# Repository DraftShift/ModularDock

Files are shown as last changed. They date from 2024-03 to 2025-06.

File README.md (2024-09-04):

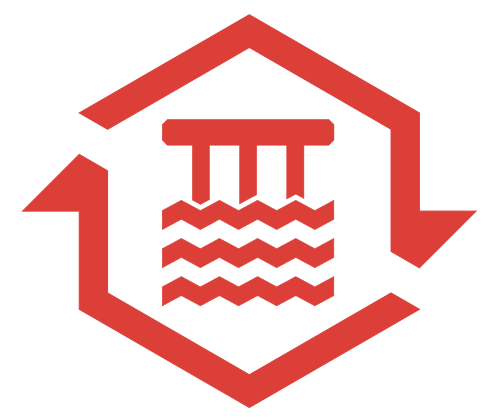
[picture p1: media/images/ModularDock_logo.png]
#  Modular Dock


&nbsp;&nbsp;&nbsp;&nbsp;&nbsp;&nbsp;


**Modular Dock for StealthChanger**

This dock is a drop in type. The back plate will allow for you to adjust the tool to be at perfect 90, I'd recommend 1 degree forward just to keep the dock in place.  Magnets are 5x2s and are optional, but recommened.

See [TODO](TODO.md) before you commit to building these.

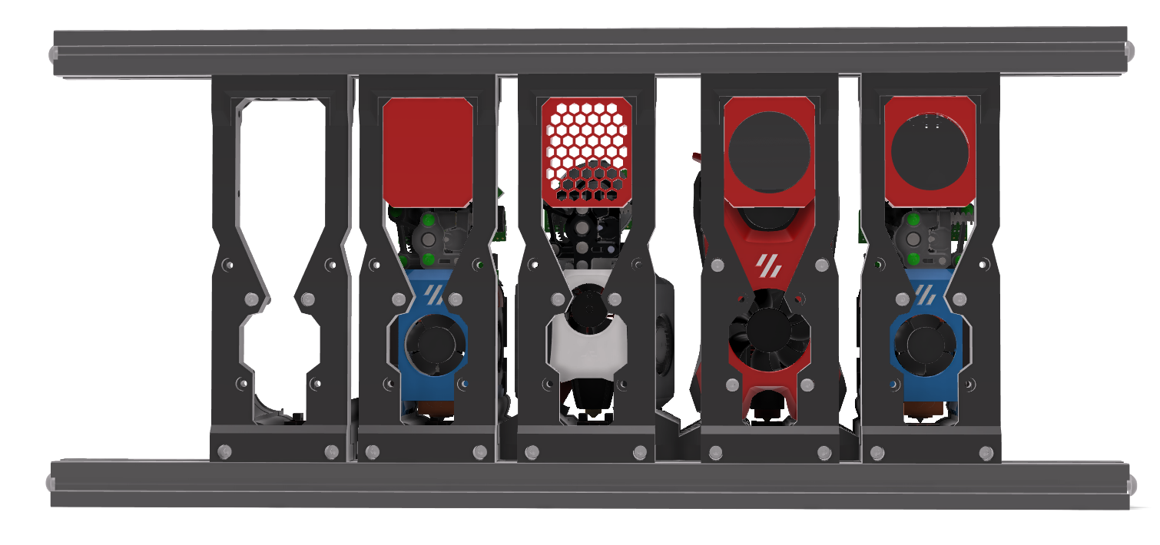
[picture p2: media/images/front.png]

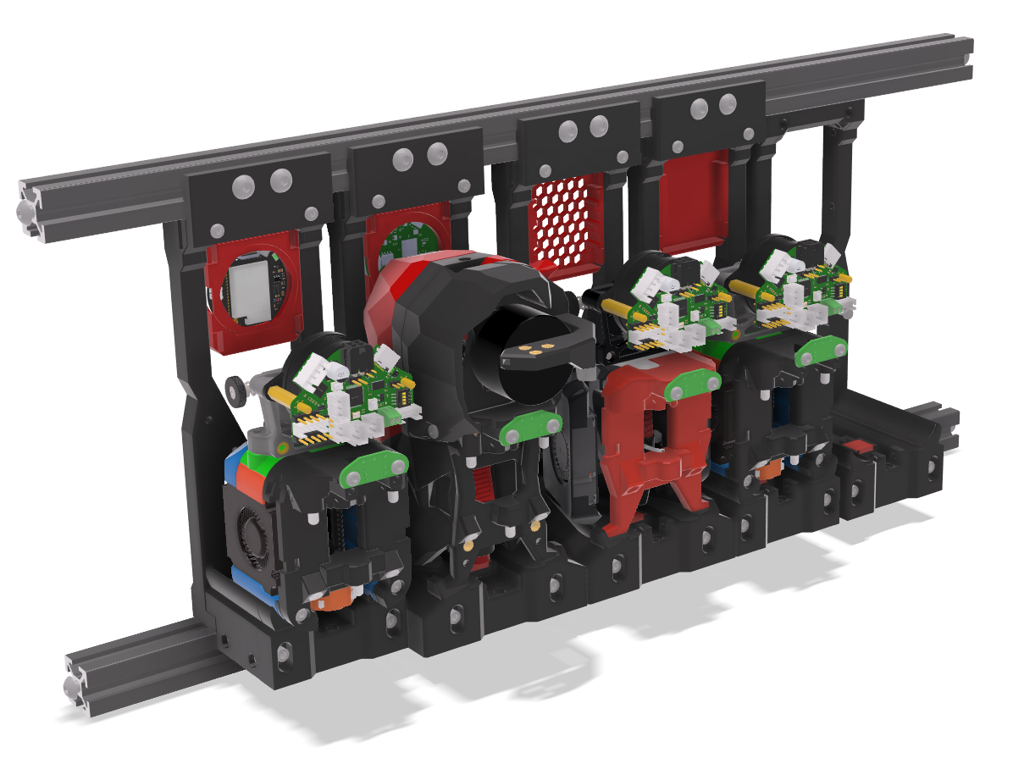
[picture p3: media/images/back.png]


### Orientation

The STLs are not already in the proper orientation

### Print list
- 1 frame (Top, Bottom, Left, Right)
- 1 frame L bracket (optional)
- 1 [tooltype] Base
- 1 [tooltype] Back [type]
- 1 Wiper [type]
- 1 Container [type] (optional)
- Combination of Links (only if not using crossbar for docks)

**NOTE: all docks must end at on the same `Y` length and `Z` height, do not mix dock lengths or heights**

**NOTE: stubby version not compatible with extended frame crossbar versions (2040 front, Door Buffer, etc)**

# BOM

[BOM](BOM.md)

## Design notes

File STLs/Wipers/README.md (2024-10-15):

Bamboo PTFE wiper based on [Bamboo clone wiper](https://www.printables.com/model/359226-bambu-lab-nozzle-wiper)

Leaving the old one here as an alternative but it's much too stiff.

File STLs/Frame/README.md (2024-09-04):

**Short frame should only be used with 1515 printers.  You can use it with 2020 but the Z requirement may pull the MGN block off the rail.  You have been warned, to be safe stick to the normal size frame unless you know what you are doing.**

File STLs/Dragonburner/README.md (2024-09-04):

- Base.stl is for all use cases

- Base_Stubby.stl is **ONLY** to be used with stock frame. ie: Top Mount or MiniBFIs, do not use with Top_Crossbar.stl, Bottom_Crossbar.stl

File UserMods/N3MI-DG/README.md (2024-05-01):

# KNOMI2 Container Mod
Allow the WIFI antenna to be mounted to the back of the container.
Added XH connector.
Added cable tie loop.
Added screws to secure the back plate.
Trimmed sides of frame at extremities of Knomi for cleaner printing.
Added extra clearance around USB port.

#### Extra BOM
2x M2x10mm Self Tapping Screws
1x XH-2A Female Connector
1x Cable Tie

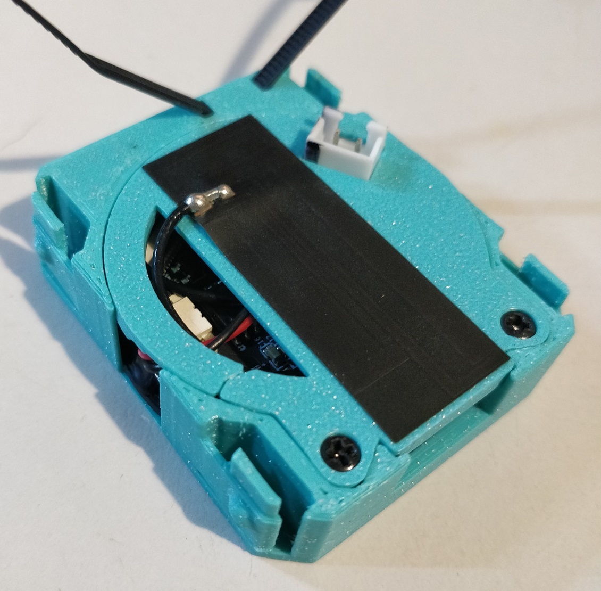
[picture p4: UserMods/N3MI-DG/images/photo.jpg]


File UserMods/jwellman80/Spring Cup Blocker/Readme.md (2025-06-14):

# Spring Cup Blocker

by [jwellman80](https://github.com/jwellman80) aka. averen on most of the Discords. 

This blocker is held up by a short piece of spring steel rather than a spring.  I found that 22mm measured from the center screw was just about right for use with the AntHead docks.  

# BOM

|Part|Amount|Description|
|:---|:----:|:---|
|Spring Steel| 1 | [Amazon](https://www.amazon.com/SunplusTrade-Stainless-Exhaust-Multi-Purpose-Locking/dp/B072WC1MXT) |
|M2x4 Screw| 1 | [Amazon](https://www.amazon.com/dp/B0C5JVC6Z3)|

The Spring Steel and Screws can likely be anything that fits.  Above is just what I used.  

# Instructions

- Cut a piece of spring steel longer than you need (makes a nice handle when filling with Silicone)
- Drill a hole through the spring steel that the screw will pass through
- Attach the spring steel to the printed part with the screw
- Fill with High Temp RTV Silicone
- Let cure 
- Mount using the [Spring Steel Body and Spring Steel Clamp](https://github.com/DraftShift/ModularDock/tree/main/STLs/Blockers) that corresponds to your docks. 

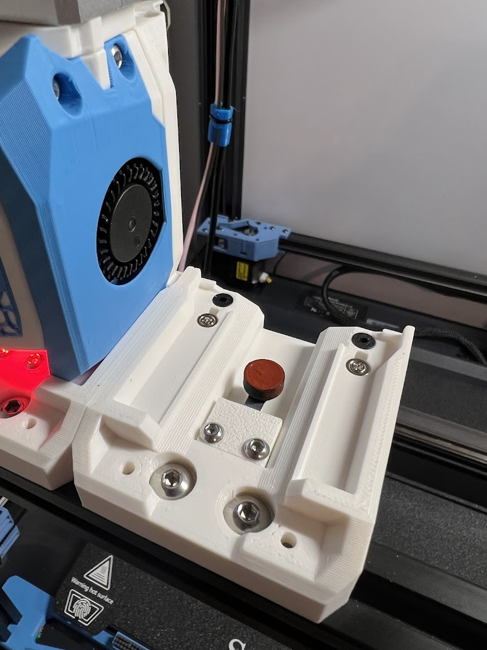
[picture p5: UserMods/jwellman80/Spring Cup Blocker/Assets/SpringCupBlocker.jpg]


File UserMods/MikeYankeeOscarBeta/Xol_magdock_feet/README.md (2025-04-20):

# XOL Magdock Feet
by [MikeYankeeOscarBeta](https://github.com/MikeYankeeOscarBeta/) (DraftShift Discord: #MikeyMike, VoronDesign Discord: #MikeyMike V2.5796, Voron Toolchangers Discord: MikeyMike - Github: [MikeYankeeOscarBeta](https://github.com/MikeYankeeOscarBeta/StealthChanger))

Megnetic dock "feet" for Xol-toolhead StealthChanger and Modular-Docks.
Improves docking/undocking reliability and keeps the toolhead from falling off or moving if you bump or flip the printer.

For further improved docking/undocking combine this mod with the Xol_magdock_adapter mod https://github.com/DraftShift/ModularDock/tree/main/UserMods/MikeYankeeOscarBeta/Xol_magdock_adapter

Individual adapters for NF (normal flow) and UHF (high/ultra high flow) versions of XOL-toolhead.

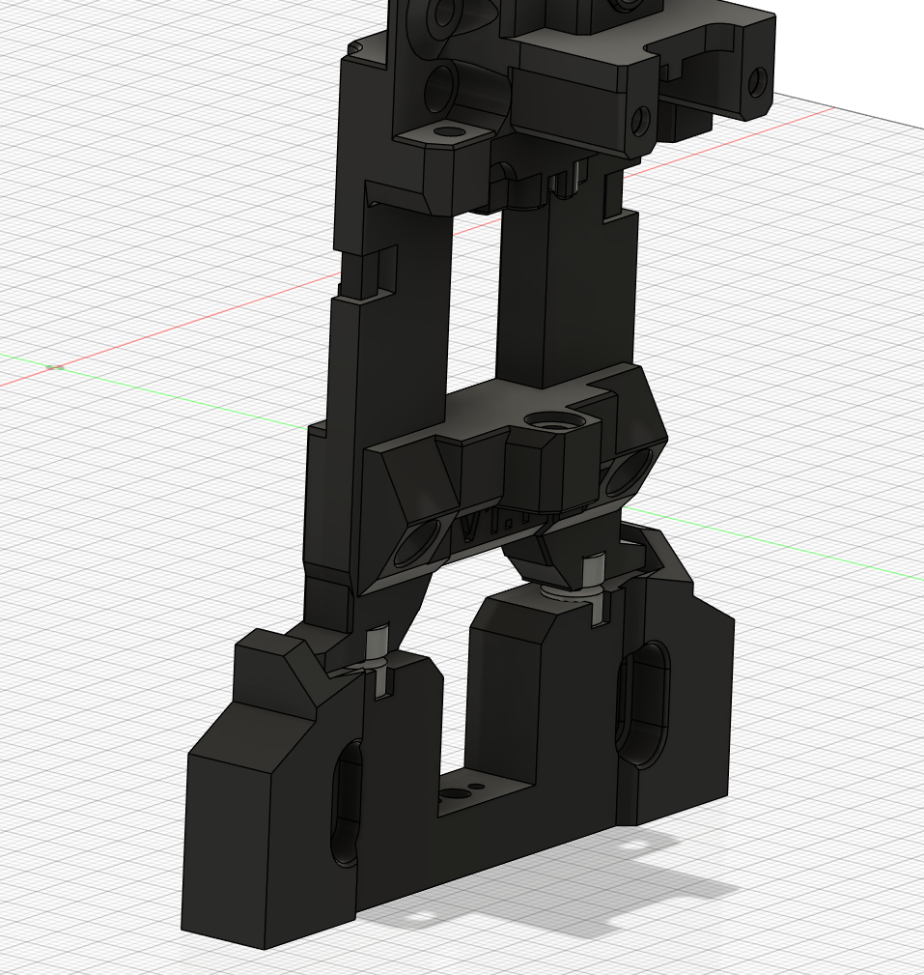
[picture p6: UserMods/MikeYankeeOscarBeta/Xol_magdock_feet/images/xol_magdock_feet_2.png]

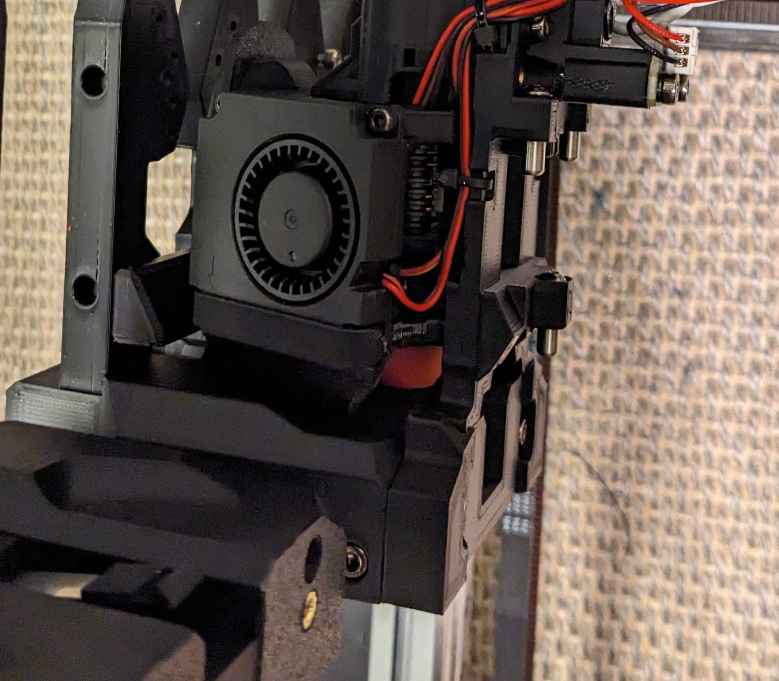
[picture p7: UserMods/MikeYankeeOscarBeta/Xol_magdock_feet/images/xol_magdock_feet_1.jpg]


## Parts to print
### NF (normal flow / "short")
- SC_XOL_nf_Feetmags.stl (replaces stealthchanger XOL_Short.stl) 
- DSD_Modular_Dock_Back_XOL_Feetmags.stl (replaces ModularDock/XOL/Back.stl)
### UHF (ultra high flow / "medium")
- SC_XOL_Feetmags_UHF.stl  (replaces stealthchanger XOL_Medium.stl) 
- DSD_Modular_Dock_Back_XOL_Feetmags.stl (replaces ModularDock/XOL/Back.stl)

## BOM additions:
| Part | Amount | Description | Link |
|---|---|---|-|
| 2x8mm FHCS self-tapping Screw  | 4 | Magnetic 2x8mm Countersunk self-tapping screw (not stainless) | https://aliexpress.com/item/1005001715736935.html |
| Countersunk m2 6x3 Magnets | 4 | Countersunk n52 magnets, but lower strength also works | https://aliexpress.com/item/1005008755692873.html  |

Alternatively you can glue in normal 6x3 magnets with a good high temperature two component epoxy (just make sure the magnets sitting perfectly flush before glueing anything in)

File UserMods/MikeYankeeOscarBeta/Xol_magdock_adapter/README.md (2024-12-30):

# XOL Magdock Adapter
by [MikeYankeeOscarBeta](https://github.com/MikeYankeeOscarBeta/) (DraftShift Discord: #MikeyMike, VoronDesign Discord: #MikeyMike V2.5796, Voron Toolchangers Discord: MikeyMike - Github: [MikeYankeeOscarBeta](https://github.com/MikeYankeeOscarBeta/StealthChanger))

Printable adapters for modular docks to get magnetic docking on XOL-toolhead.

Individual adapters for NF (normal flow) and UHF (high/ultra high flow) versions of XOL-toolhead.

## BOM:
| Part | Amount | Description |
|---|---|---|
| M3x8mm SHCS Screw | 2 | M3 screw, BHCS will also work |
| 6x3 Magnets | 4 | reccommend n52 magnets, but lower strength also works |

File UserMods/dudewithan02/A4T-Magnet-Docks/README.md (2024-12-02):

# STEALTHCHANGER A4T MAGNETIC DOCKS

Magnet dock uprights to work with Stealthchanger Modular Docks to allow for the addition of A4T ([A]nother [4]010 [T]oolhead) by [Armchair Heavy Industries](https://github.com/Armchair-Heavy-Industries/A4T).

These dock uprights use 4 6x3mm N52 magnets to allow for 4 magnetic contact points between the dock and the toolhead.

**"But wait!! A4T only has 2 accessible screws on the front face of the toolhead!"** Correct! So I added 2 M3.5mm (yes, M3.5!) grub screws into the upper Allen key access holes to give two more magnetic contact points

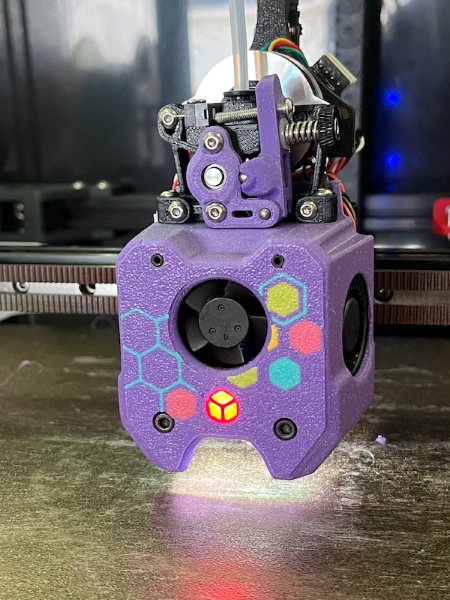
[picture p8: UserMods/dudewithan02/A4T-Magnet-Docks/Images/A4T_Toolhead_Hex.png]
A4T_toolhead_hex_pattern


## BOM (Per Toolhead)

| Item | QTY | Link (non-affiliate) |
| --- | --- | --- |
| Magnet 6x3mm N52 |  4  | [Ali Express: HKHK Store](https://www.aliexpress.com/item/1005001542593396.html)
| M3.5 x 8mm grub screw **Magnetic!** |  2  | [Ali Express: LIYA Hardware](https://www.aliexpress.com/item/32865464785.html)
| M3 x 45mm SHCS **Magnetic** |  2  | [Ali Express: LIYA Hardware](https://www.aliexpress.com/item/32810872544.html)
| M3 x 12mm SHCS |  4  | [Ali Express: LIYA Hardware](https://www.aliexpress.com/item/32810872544.html)

**Note:** If you've already built your A4T toolhead and you used magnetic screws for the main lower mounting screws then you don't need to order extra M3x45mm screws, otherwise you will need the screws from the above BOM.

## ASSEMBLY AND SETUP

1. Assemble your A4T toolhead as per normal, making sure to use the magnetic M3x45mm lower screws to attach the A4T cowl to the Stealthchanger A4T backplate.

2. Check that the upper cowl mounting screws are tight, then thread in the two M3.5mm grub screws, and screw them in until they're flush with the front face of the cowl.

3. Press in 4 6x3mm magnets into the dock uprights. You may need to use superglue to keep them in place.

4. Optional: There are holes to thread in M3x12mm SHCS to allow for some adjustment of the magnet positions. I'm not using any, and my docking movements are smooth, but YMMV.

5. Continue to assemble the docks as per the [Stealthchanger Modular Dock manual](https://github.com/DraftShift/ModularDock/tree/main/Manual).

6. Set your dock park positions as you normally would as per the [Stealthchanger wiki](https://github.com/DraftShift/StealthChanger/blob/main/wiki/Calibration.md)

Modular Dock with A4T magnetic uprights:
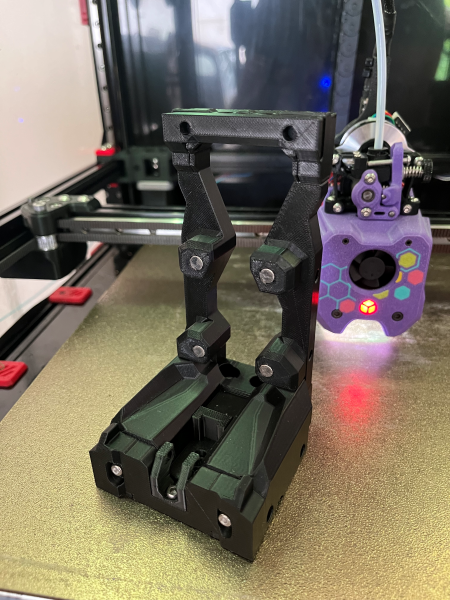
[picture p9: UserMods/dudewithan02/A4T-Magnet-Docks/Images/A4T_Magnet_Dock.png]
A4T_dock_assembled


## FAQ
- **What Stealthchanger dock system does this work with?** This is compatible with Stealthchanger Modular Docks
- **Does this suit the long or short dock option?** At this point I've only been working with the short docks on my build, I've got no intention of making this work for the long dock system unless people ask for it.

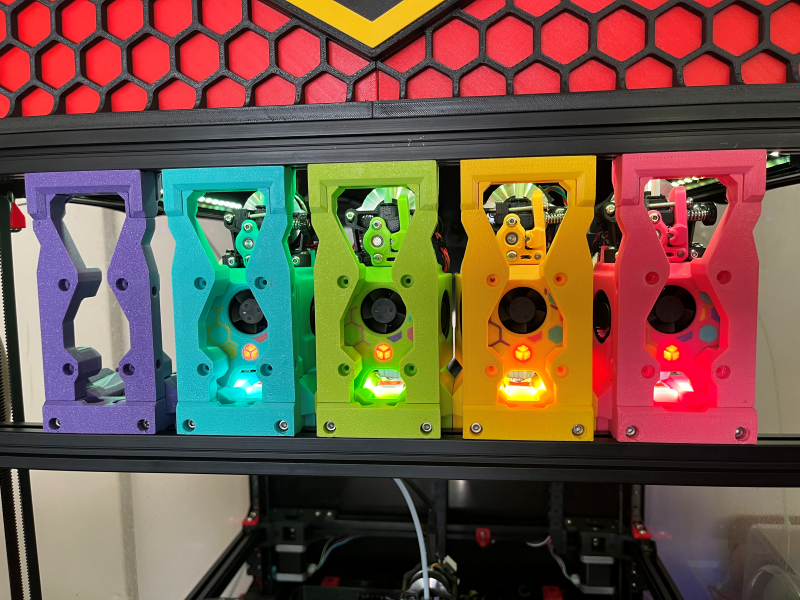
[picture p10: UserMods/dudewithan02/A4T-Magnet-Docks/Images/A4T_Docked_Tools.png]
A4T_docked_tools


## CREDITS

Credit goes to the hard work by the people at DraftShift Design for their work on the Stealthchanger Voron toolchanger project, and DW-Tas at Armchair Heavy Industries for all the work on A4T!.

[DraftShift Design](https://github.com/DraftShift)

[Armchair Heavy Industries](https://github.com/Armchair-Heavy-Industries)

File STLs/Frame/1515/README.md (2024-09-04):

- Top.stl, Bottom.stl: Use with Top Mounting or stock frame with or without crossbar (ie: MiniBFIs)

- Top_Crossbar.stl, Bottom_Crossbar.stl: Use with extended frame with crossbar (ie: 2040 front, Door Buffer)

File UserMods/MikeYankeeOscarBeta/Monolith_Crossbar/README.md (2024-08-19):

# Monolith_Crossbar
by [MikeYankeeOscarBeta](https://github.com/MikeYankeeOscarBeta/) (VoronDesign Discord: #MikeyMike V2.5796, Voron Toolchangers Discord: MikeyMike - Github: [MikeYankeeOscarBeta](https://github.com/MikeYankeeOscarBeta/StealthChanger))

DraftShiftDesign Discord - user-project thread:    https://discord.com/channels/1226846451028725821/1243948065208008705

### Only compatible with 4040 or 2040 front vertical frame extrusions
### Only tested with R0 Printed Monolith AWD (pre-live shaft version)

Printable adapters for crossbar to clear monolith AWD front motors for Voron V2 with StealthChanger

Have to cut the 2020 to size.
The monolith AWD motors take 45mm on each side so the 2020 has to be 90mm shorter than the frames horizontal extrusions

## BOM:
| Part | Amount | Description |
|---|---|---|
| M3 T-slot nut | 4 | Any M3 2020 T-Slot Nut will work (recommend springnuts) |
| M5x20mm SHCS Screw | 2 | M5 SHCS socket head screw, 20mm minimum (longer is better if you can tap the extrusion deeper than 10mm) |
| M3x25mm SHCS Screw | 4 | M3 screw, BHCS will also work |
| 2020 extrusion | 1 | 2020 extrusion cut to length (see table below), tapped on both ends. Misumi#: HFS5-2020-380-TPW  / HFSB5-2020-380-TPW |
| M3x25mm SHCS Screw | 4 | M3 screw, BHCS will also work |

### Extrusion lengths for Stock V2 sizes:
| Model | Calculation | Monolith AWD Crossbar extrusion length |
|---|---|---|
| Voron V2-350 | 470.00 mm - 90mm | 380 mm |
| Voron V2-300 | 420 mm - 90mm | 330 mm |
| Voron V2-250 | 370 mm - 90mm | 280 mm |
| Voron V2-custom size  | [horizontal extrusion length] - 90mm | x mm |

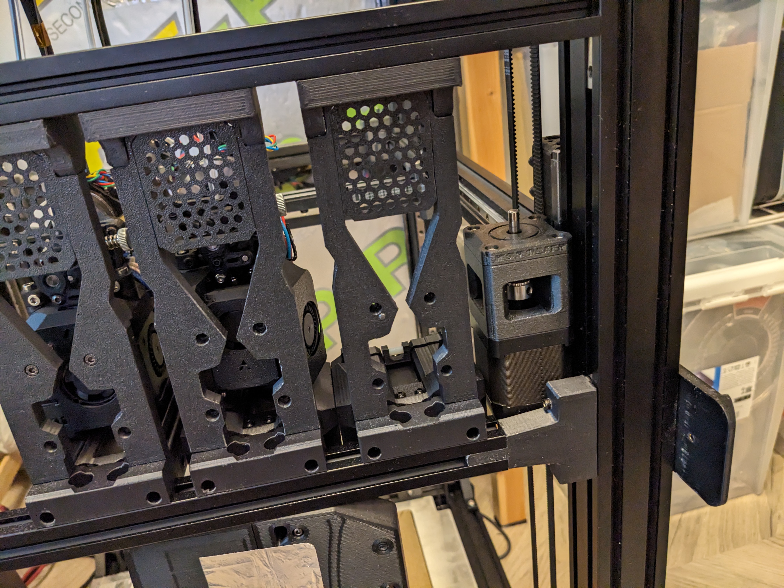
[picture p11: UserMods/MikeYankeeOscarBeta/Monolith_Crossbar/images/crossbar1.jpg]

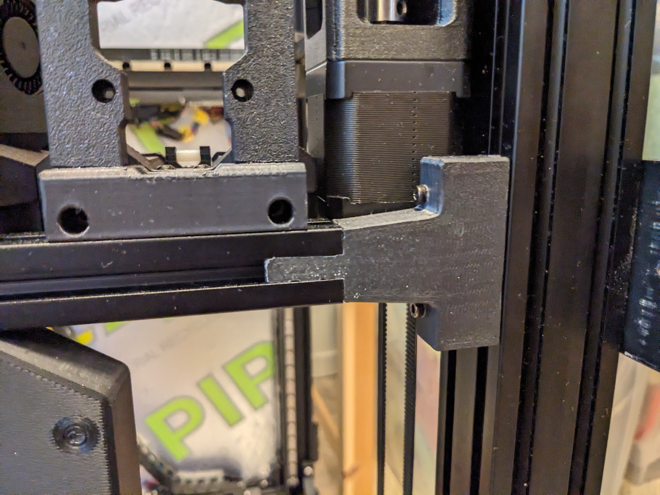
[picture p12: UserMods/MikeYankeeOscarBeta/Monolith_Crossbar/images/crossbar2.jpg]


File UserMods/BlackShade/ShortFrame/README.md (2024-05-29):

# ShortFrame

### Not compatible with Door Buffer

Modified left and right part of the frame so less Z space is used. Total Z height is reduced from 169.9mm* to 155.9mm*. Everything else stays the same. **But you need to use Tophat**

### Using SB is supported only with special docking path which is bellow
```
params_shortframe_path: [{'y':10.50 ,'z':6}, {'y':8.50, 'z':2}, {'y':5.5, 'z':0}, {'z':0, 'y':0, 'f':0.5}, {'z':-10, 'y':4}, {'z':-10, 'y':20}]
```

( \* measured between top extrusion and the crossbar )

## Support for these are not handled by the StealthChanger Team, it is handled by BlackShade on discord
##  All docks must use the same height, DO NOT MIX AND MATCH

### My discord: `blackshade`

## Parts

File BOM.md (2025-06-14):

# BOM

## Frame
**NOTE: Short frame can only be used with short frame, do NOT mix and match**

**NOTE: Short frame not compatible with taller tools**

- 6 x M3 Heatset
- 4 x M3x16 SHCS
- 4 x M5x10 BHCS `M3x8 for 1515`
- 4 x M5 T-Nut `M3 for 1515` `Only 2 if using Links`

### Links
**NOTE: Only if using one mounting bar (top or bottom)**

- 2 x M5 Nut `M3 for 1515`

### L Bracket
**NOTE: Recommended if top mounting**

- 2 x M3 Heatset
- 2 x M3x16 SHCS
- 2 x M5x10 BHCS `M3x8 for 1515`

## Base
**NOTE: Stubby base can only be used with stubby base, do NOT mix and match**

- 4 x M3 Heatset
2 x M3x20 SHCS 
2 x M3x50 SHCS `40mm for stubby`

## Back
- 1 x M3 Heatset `Optional for PTFE wiper`
- 2 x 3x6 Magnet `Optional for under tray`
- 2 x M3x10 SHCS

## Wiper
**NOTE: Only pick one type of Wiper**

- 4 x M3 Heatset
- 4 x M3x30 SHCS `20mm for DB/Yavoth`
- RTV High Temp Silicon

### Spring Steel
- 2 x M3 Heatset
- 2 x M3x8 BHCS
- 1 x 7.2x34mm Spring Steel (Old tape measure) `22mm for stubby`

### Cup
- 1 x M3 Heatset
- 1 x M3x16 BHCS
- 1 x M4 Spring cut to 2mm height `Stiffer is better`

### PTFE
**NOTE: Optional addon for all wiper types**

- 1 x M3x6 BHCS
- 1 x 15mm 4mm OD PTFE tube

## Docking
**NOTE: Docking bolts and tool cowl bolts should be magnetic steel, not Stainless if using magnets**

**NOTE: Bolts used might vary depends on base use (Stubby will be much shorter) and Cowls used**

### SB Docking
- 2 x 5x2 Magnets `Optional but recommended`
- 2 x M3x16 BHCS

### DB/Yavoth Docking
- 2 x 5x2 Magnets `Optional but recommended`
- 2 x 6x3 Magents `For Yavoth`
- 2 x M3x16 BHCS

### BB Docking
- 2 x 5x2 or 6x3 Magnets `Optional but recommended` `Use steel bolts on the top fan bolts aswell`
- 2 x M3x12 SHCS `from inside of frame`

### XOL Docking
- 2 x 5x2 or 6x3 Magnets `Optional but recommended` `Use steel bolts on the top fan bolts aswell`
- 2 x M3x12 SHCS `from inside of frame`

### MiniSB Docking
- 2 x 5x2 Magnets `Optional but recommended`
- 2 x M3x16 BHCS

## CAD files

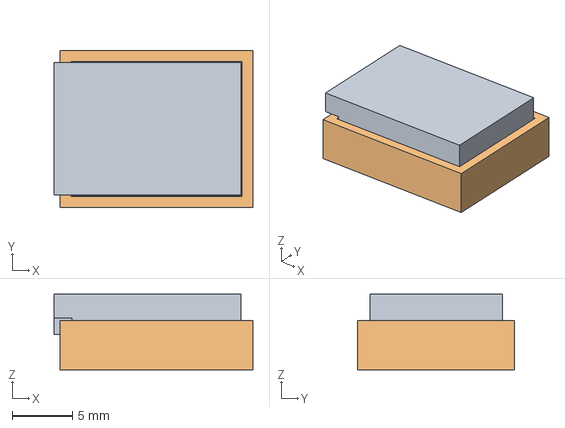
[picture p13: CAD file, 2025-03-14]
CAD/Spring Steel Pad Mold.step
16.5 x 13.0 x 6.27 mm

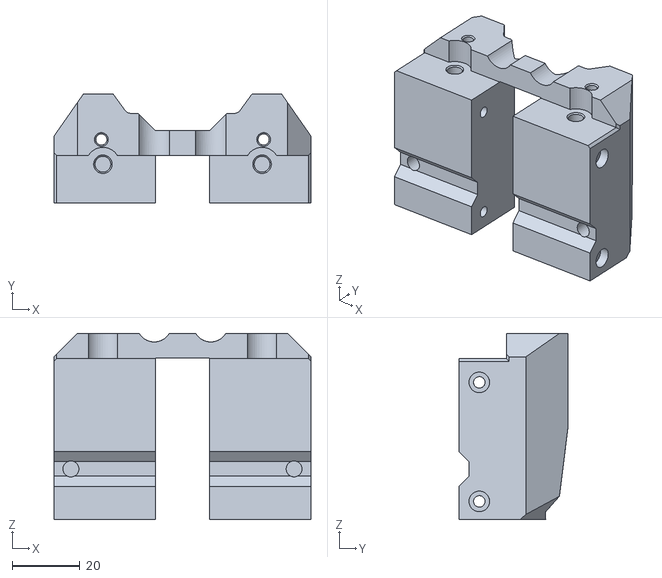
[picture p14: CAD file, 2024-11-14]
STLs/A4T/Base.stl
76.0 x 32.2 x 55.1

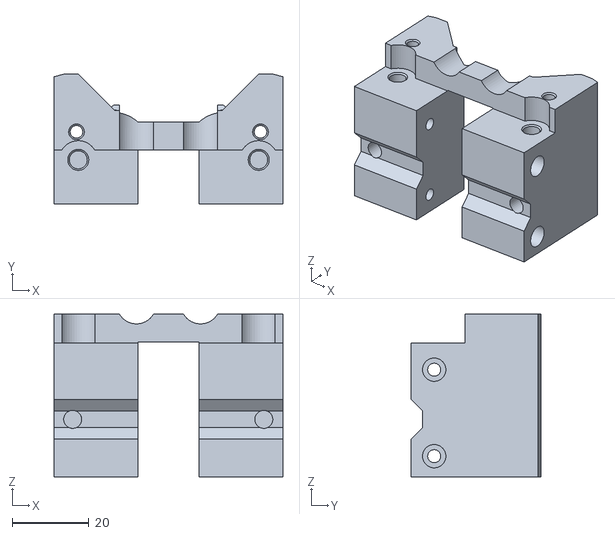
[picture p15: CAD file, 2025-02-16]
STLs/Anthead/Base_Stubby.stl
59.7 x 33.8 x 42.5

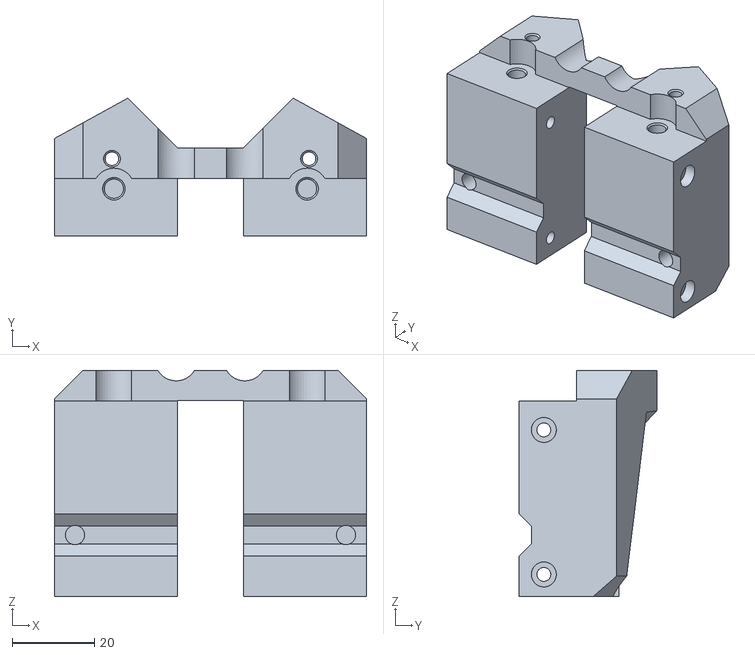
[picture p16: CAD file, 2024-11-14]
STLs/Blackbird/Base.stl
76.0 x 33.5 x 55.1

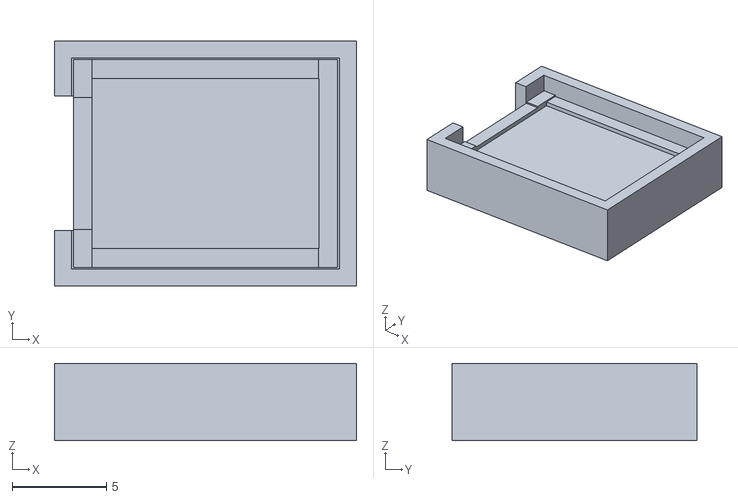
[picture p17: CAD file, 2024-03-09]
STLs/Blockers/Spring Steel Pad Mold/Nozzle Pad Mold A.stl
16.0 x 13.0 x 4.10

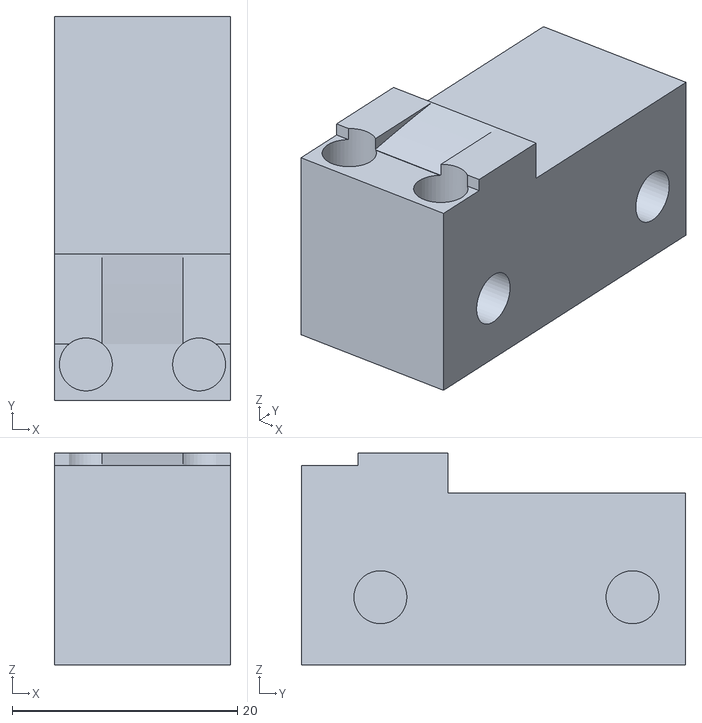
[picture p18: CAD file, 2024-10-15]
STLs/Blockers/Spring_Steel_Stubby_Body.stl
15.6 x 34.1 x 18.8

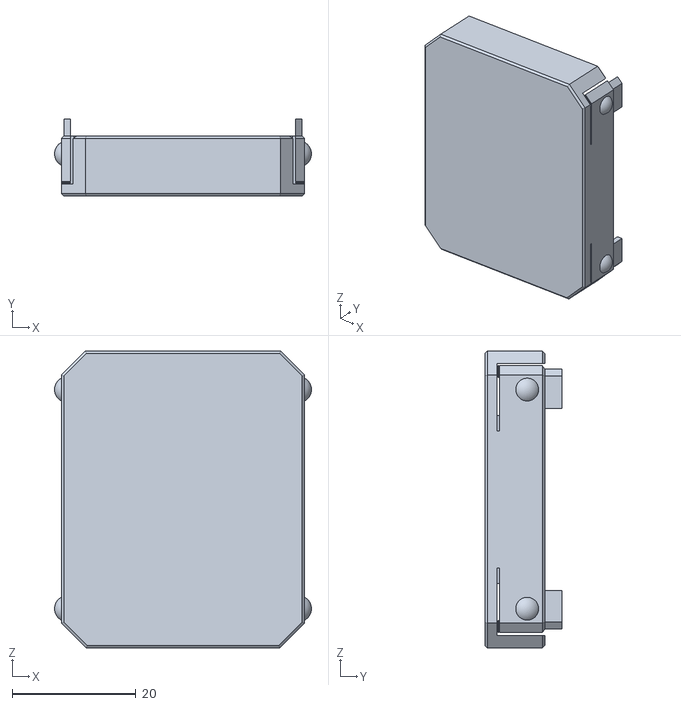
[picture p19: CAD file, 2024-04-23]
STLs/Container/[a]_Blank.stl
41.5 x 12.5 x 48.0

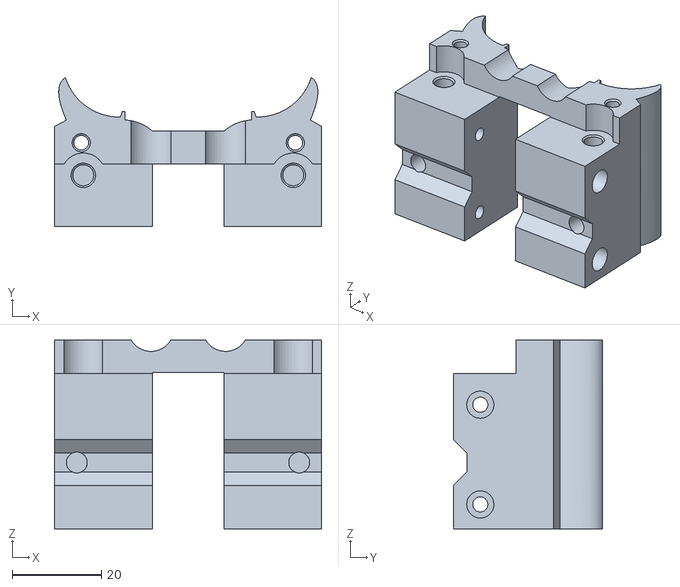
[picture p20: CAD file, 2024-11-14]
STLs/Dragonburner/Base_Stubby.stl
59.9 x 33.4 x 42.4

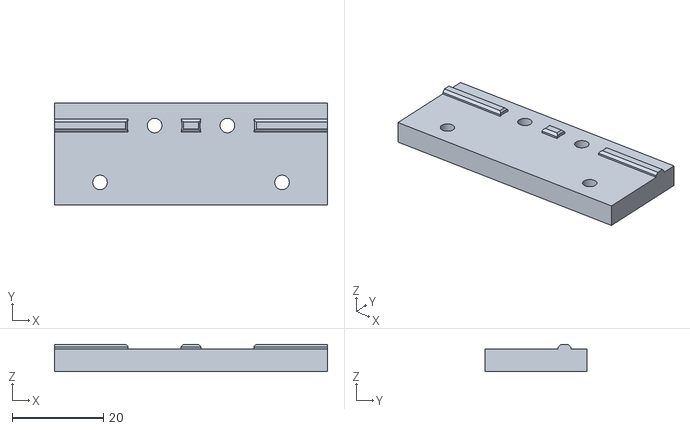
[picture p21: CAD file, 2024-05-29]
STLs/Frame/1515/L_Bracket.stl
60.0 x 22.5 x 6.00

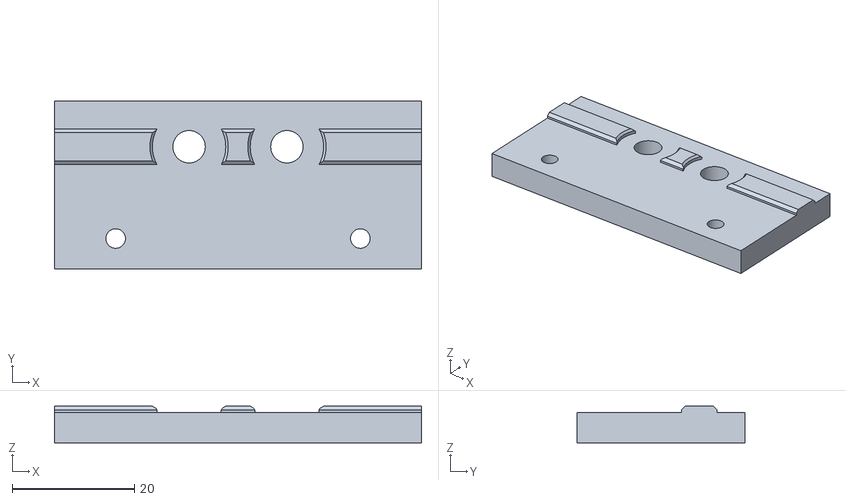
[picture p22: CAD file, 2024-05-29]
STLs/Frame/2020/L_Bracket.stl
60.0 x 27.5 x 6.00

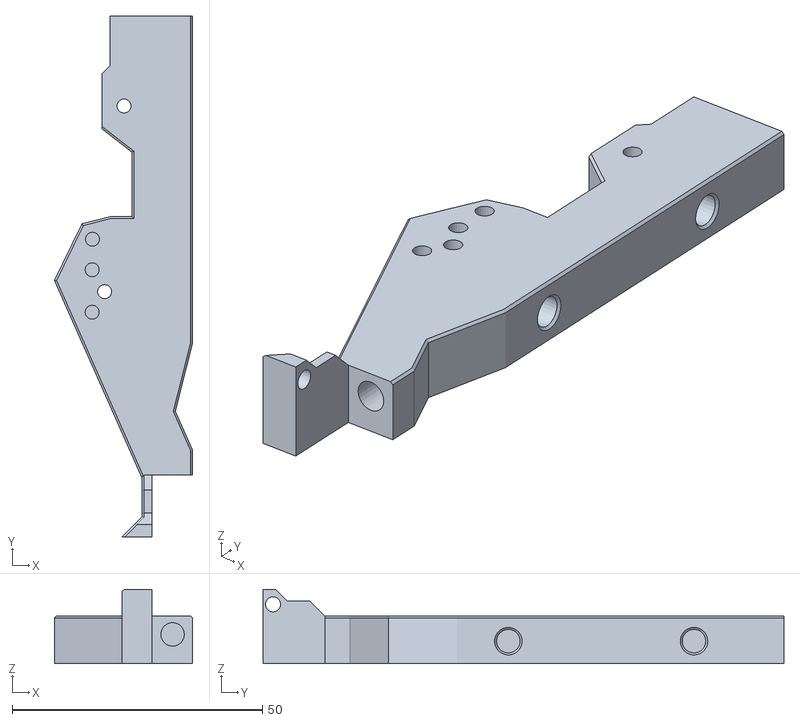
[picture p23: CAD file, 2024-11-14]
STLs/Frame/Right_Short.stl
27.6 x 104.1 x 14.8

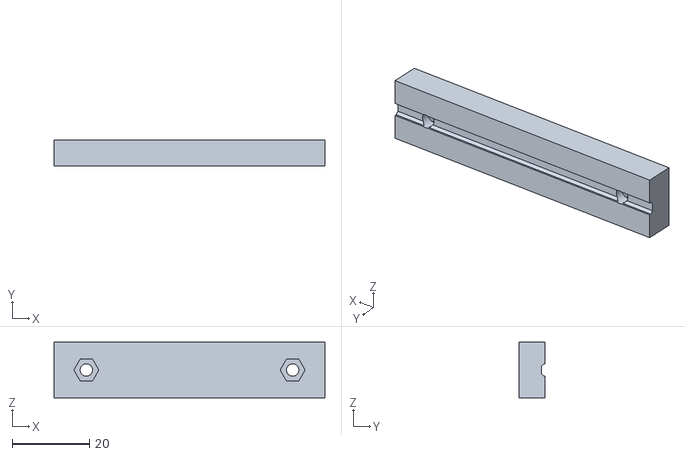
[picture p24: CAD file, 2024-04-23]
STLs/Links/1515/80_to_60.stl
70.0 x 6.80 x 14.4

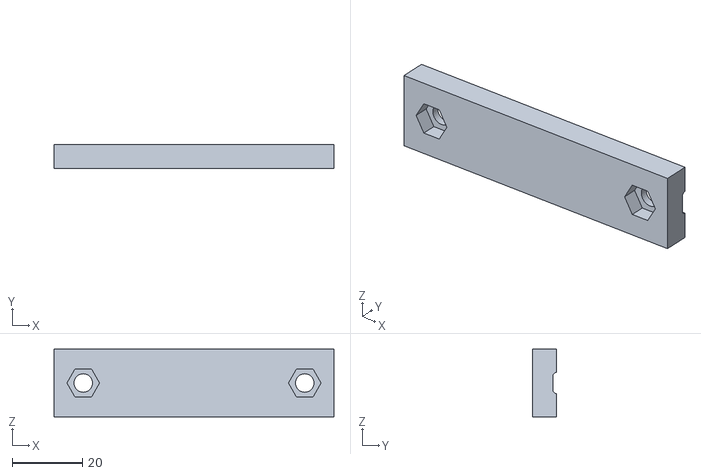
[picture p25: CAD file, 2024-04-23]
STLs/Links/2020/80_to_80.stl
80.0 x 6.80 x 19.4

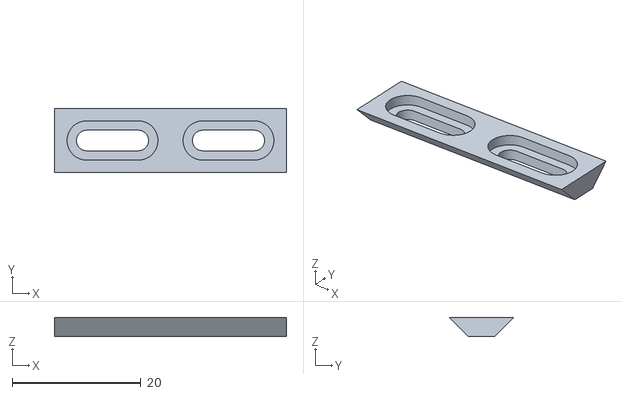
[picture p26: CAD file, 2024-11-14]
STLs/Links/Rear.stl
36.0 x 10.00 x 3.00

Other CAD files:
STLs/MiniSB/Base_Stubby.stl
STLs/Stealthburner/Base.stl
STLs/Wipers/BambuNozzleWiper.step
STLs/XOL/Base.stl
CAD/Links.step
STLs/A4T/Back.stl
STLs/Anthead/Back.stl
STLs/Anthead/Base.stl
STLs/Blackbird/Back.stl
STLs/Blockers/Cup.stl
STLs/Blockers/Cup_Body.stl
STLs/Blockers/Cup_Stubby_Body.stl
STLs/Blockers/Spring Steel Pad Mold/Nozzle Pad Mold B.stl
STLs/Blockers/Spring_Steel_Body.stl
STLs/Blockers/Spring_Steel_Clamp.stl
STLs/Container/[a]_Grill.stl
STLs/Container/[a]_Knomi.stl
STLs/Container/[a]_Knomi2.stl
STLs/Container/[a]_Knomi2_Ring.stl
STLs/Container/[a]_Knomi_Ring.stl
STLs/Dragonburner/Back.stl
STLs/Dragonburner/Back_Legacy.stl
STLs/Dragonburner/Base.stl
STLs/Frame/1515/Bottom.stl
STLs/Frame/1515/Bottom_Crossbar.stl
STLs/Frame/1515/Top.stl
STLs/Frame/1515/Top_Crossbar.stl
STLs/Frame/2020/Bottom.stl
STLs/Frame/2020/Bottom_Crossbar.stl
STLs/Frame/2020/Top.stl
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

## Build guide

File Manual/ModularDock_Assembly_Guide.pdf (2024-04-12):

# DRAFTSHIFT DESIGN

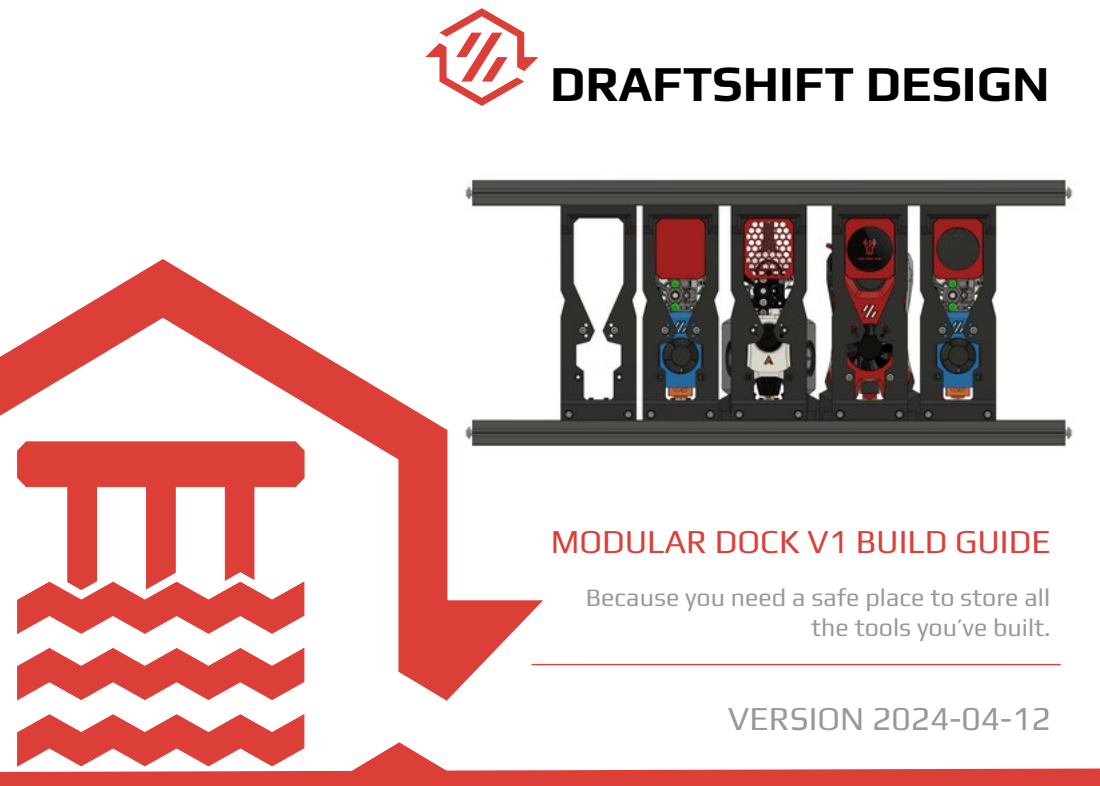
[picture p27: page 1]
VERSION 2024-04-12

MODULAR DOCK V1 BUILD GUIDE

Because you need a safe place to store all

the tools you’ve built.

## PREFACE

Before you begin on your journey, a word of caution.

In the comfort of your own home you are about to assemble a robot. This machine can maim, burn, and electrocute you if you are not careful. Please do not become the first STEALTHCHANGER fatality. There is no special Reddit flair for that.

Please, read the entire manual before you start assembly. As you begin wrenching, please check our Discord channels for any tips and questions that may halt your progress.

Most of all, good luck!

THE DRAFTSHIFT DESIGN TEAM

2

## GITHUB.COM/DRAFTSHIFT/MODULARDOCK

## TABLE OF CONTENTS

Introduction | 04
Hardware | 07
Frame | 08
Base | 10
Back Plate | 12
Wipers | 13
Install | 15
Containers | 17
Setup Tool | 18
Next Steps | 19

3

## INTRODUCTION

PART PRINTING GUIDELINES

The Voron Team has provided the following print guidelines for you to follow in order to have the best chance at success with your parts. The StealthChanger Team recommends to follow the same standards. There are often questions about substituting materials or changing printing standards, but we recommend you follow these:

3D PRINTING PROCESS
Fused Deposition Modelling (FDM)

MATERIAL
ABS

LAYER HEIGHT
Recommended: 0.2mm

EXTRUSION WIDTH
Recommended: Forced 0.4mm

INFILL TYPE
Grid, Gyroid, Honeycomb, Triangle or Cubic

INFILL PERCENTAGE
Recommended: 40%

WALL COUNT
Recommended: 4

SOLID TOP/BOTTOM LAYERS
Recommended: 5

4

## INTRODUCTION

FILE NAMING

By this time you should have already downloaded our STL files from the StealthChanger GitHub. You might have noticed that we have used the Voron naming convention for the files. This is how to use them.

PRIMARY COLOUR

Example part_x4.stl

These files will have nothing at the start of the filename.

ACCENT COLOUR

Example [a]_part.stl

We have added “[a]” to the front of any STL file that is intended to be printed with accent colour.

QUANTITY REQUIRED

Example [a]_part_x4.stl

If any file ends with “_x#”, that is telling you the quantity of that part required to build the machine.

HOW TO GET HELP

If you need assistance with your build, we are here to help. Head on over to our Discord group and post your questions. This is our primary medium to help STEALTHCHANGER Users and we have a great community that can help you out if you get stuck.

5

### https://discord.gg/jJs73c6vSc

## INTRODUCTION

REPORTING ISSUES

Should you find an issue in the documentation or have a suggestion for an improvement please consider opening an issue on GitHub (https://github.com/DraftShift/ModularDock/issues). When raising an issue please include the relevant page numbers and a short description; annotated screenshots are also very welcome. We periodically update the manual based on the feedback we get.

THIS IS JUST A REFERENCE

This manual is designed to be a simple reference manual. Building a StealthChanger can be a complex endeavour and for that reason we recommend downloading the CAD files off our Github repository if there are sections you need clarification on. It can be sometimes be easier to follow along when you have the whole assembly in front of you.

### https://github.com/DraftShift/ModularDock

6

## HARDWARE REFERENCE

BUTTON HEAD CAP SCREW (BHCS) Metric fastener with a domed shape head and hex drive. Most commonly found in locations where M5 fasteners are used. ISO 7380-1 | SOCKET HEAD CAP SCREW (SHCS) Metric fastener with a cylindrical head and hex drive. The most common fastener used on the Voron. ISO 4762
FLAT HEAD COUNTERSUNK SCREW (FHCS) Metric fastener with a cone shaped head and a flat top. ISO 10642 | HEAT SET INSERT Heat inserts with a soldering tip so that they melt the plastic when installed. As the plastic cools, it solidifies around the knurls and ridges on the insert for excellent resistance to both torque and pull-out.
MAGNET Metric round button neodymium magnet. | SPRING Small stiff spring, be prepared to cut to fit.
HIGH TEMP RTV SILICON High Temp RTV Silicon in a tube for making moulds, make sure it can handle the temp of the nozzle. | T-NUT A type of nut that slides into the extrusion rail as a method of affix other parts to it.

HEX NUT Metric hex nut used with metric fasteners.

7

## FRAME

8

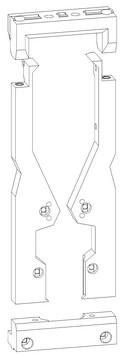
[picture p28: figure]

## Heat Set

INSERT HEAT SETS

Start by setting the heat sets.

PARTS

The parts required to build a frame, Top, Bottom, Left and Right.

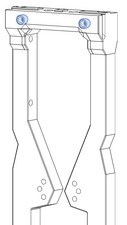
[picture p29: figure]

OPTIONAL INSERT HEAT SETS

Optionally add these inserts when using the “L Bracket”, recommended if top mounting.

## FRAME

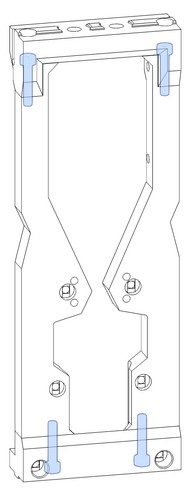
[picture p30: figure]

ASSEMBLE

Use M3x16mm socket head screws to attach the top and bottom to the frame sides. Make sure to get them straight and tight.

## M3x16mm SHCS

9

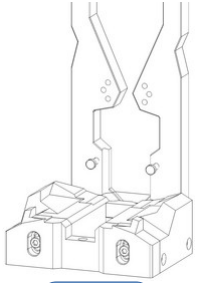
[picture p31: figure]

BASES

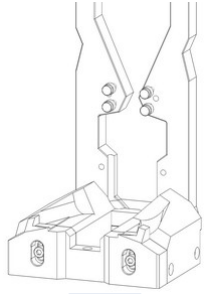
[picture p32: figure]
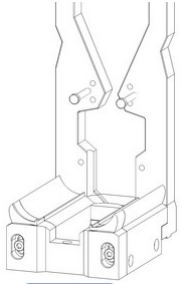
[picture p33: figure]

The modular dock has lots of options. This is to support different types of tools as well as a variety of nozzle blockers and wipers when at rest. Since the assembly is all the same we will only show the stealthburner. But rest assured they all use the same hardware and process.

NOTE: stubby version can not be used with extended front frame, 2020 front frame only.

NOTE: stubby version can not be used with any other tools, so if you choose the stubby version you can only use dragonburners and stubby docks. Also the bolts are slightly shorter see the BOM.

## BASE

10

Stealthburner | Dragonburner | Blackbird

## BASE

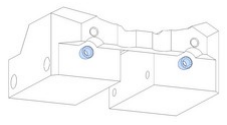
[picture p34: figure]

INSERT HEAT SETS

Start by setting the heat sets.

ATTACHING TO FRAME

Insert the bolts from the front of the dock and snug them. Then install the longer bolts via the back of the base and tighten. Then return to the front and tighten.

NOTE: 40mm screws are used in place of the 50mm for the stubby version.

## Heat Set

11

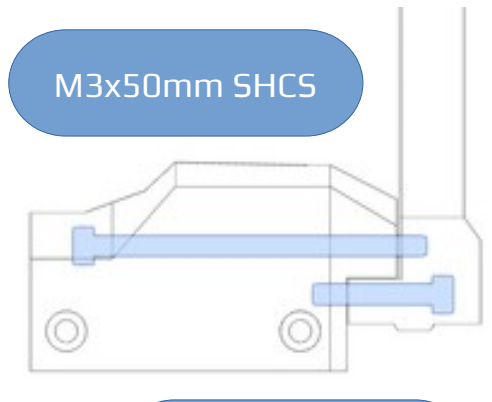
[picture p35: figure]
M3x50mm SHCS

## M3x20mm SHCS

## BACK PLATE

12

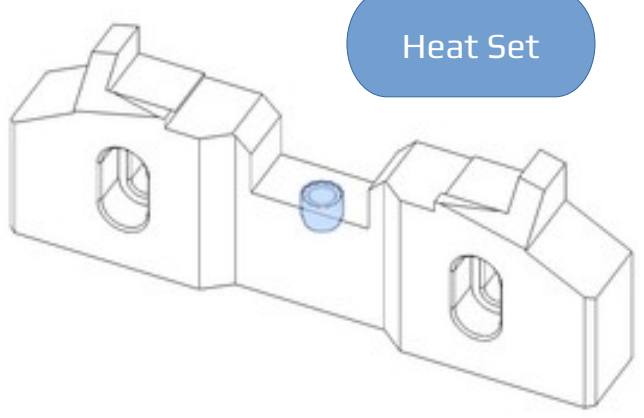
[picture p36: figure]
Heat Set

OPTIONAL HEAT SET

Optional heat set for PTFE wiper install.

NOTE: There are 2 optional 6x3 magnets on the bottom for future options to attach to.

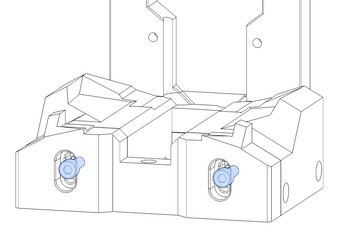
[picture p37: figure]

## M3x10mm SHCS

INSTALL BACK PLATE

Screw the back plate on, just snugging it up as we will adjust this later in the manual.

13

## WIPERS

WIPERS

Just like bases, wipers have options. The main ones are Cup or Spring Steel version. Both were designed by TapChanger and adopted for these docks.

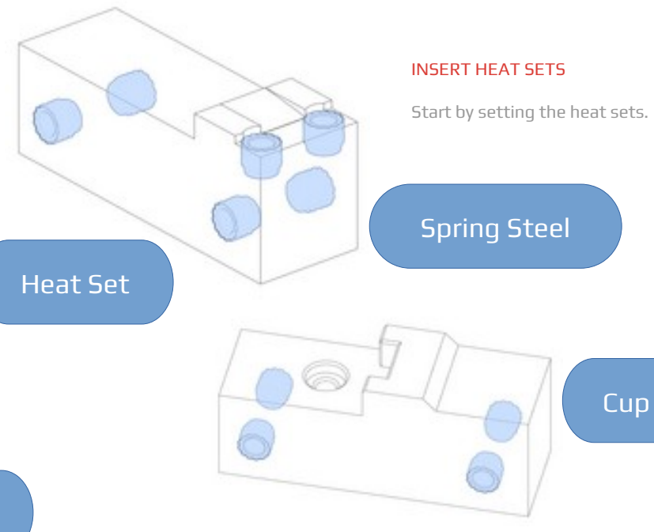
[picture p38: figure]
INSERT HEAT SETS; Start by setting the heat sets.; Heat Set; Spring Steel

## Cup Style

M3x6mm BHCS | M3x16mm BHCS + M4 Spring
Spring Steel | Cup Style

INSTALL BLOCKER

Both types will require High Temp RTV Silicon moulds.

CUP: Install the heat set from the bottom of the cup, install an M3 screw from the bottom to be flush, then fill the cup with silicon and with a wet finger press it smooth and let it dry then install, cut the spring to be about 2-3mm high.

SPRING STEEL: Use the provided mould, fill both sides with silicon, insert the spring steel and close the mould. Let dry and install.

14

## WIPERS

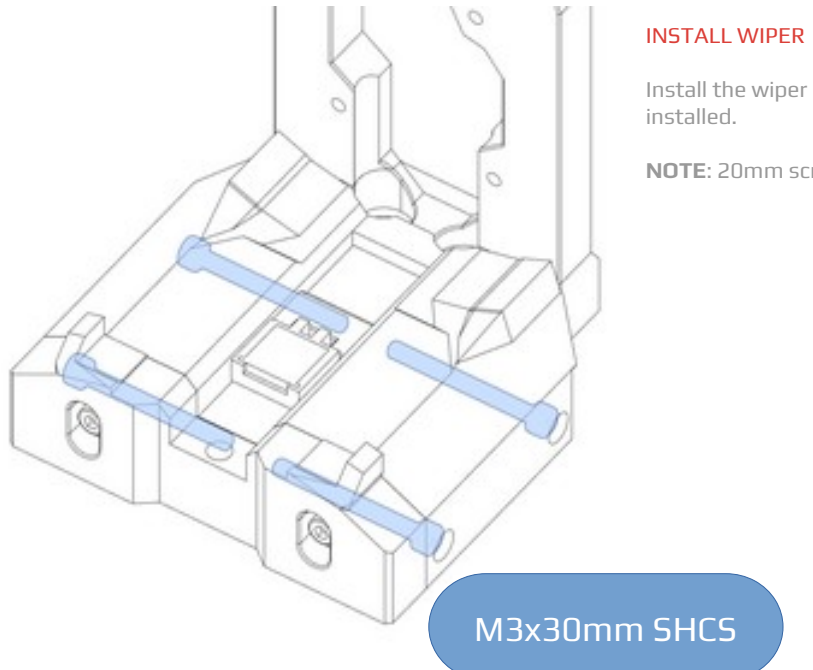
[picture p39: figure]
M3x30mm SHCS; INSTALL WIPER; installed.

OPTIONAL PTFE WIPER

Cut a 8mm piece of 4mm OD PTFE tube. Fit between the 2 holes and screw in an M2.5x6mm (2mm ID) or M3x6mm FHCS (3mm ID) screw to each end to hold the PTFE tube in place.

Install the assembled wiper onto the back plate.

Install the wiper into the base of the dock. Seen here with the back plate already

NOTE: 20mm screws used for DB width docks.

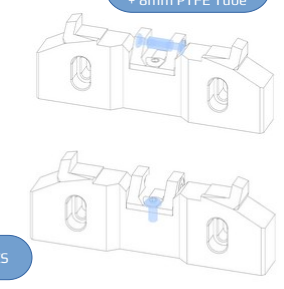
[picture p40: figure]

## M3x6mm BHCS

## 6mm FHCS + 8mm PTFE Tube

## MOUNTING

L BRACKET

Once you have the docks mounted to the top bar, add 2 more M5 T-Nuts to the inside of the top rail. Using M5 BHCS to the rail and M3 BHCS to the attach the bracket to the dock.

MOUNTING OPTIONS

Like most parts of the modular dock, you have options at this point.

- Top mount, this meant only mounting to the top bar of the frame. In this configuration, you should use the “L Bracket” and the bottom “Links”.
- Bottom mount or Crossbar Mount, this means you are only mounting to a bar that runs in parallel to the top frame bar, but at least 170mm lower. In this configuration nothing is mounted to the top and no extras are required.
- Full mount, this means you are running both top and bottom bars to mount to. This is the most solid option and the most solid by far. You do not need any extra brackets.

The guide will go over all the options, but you will not need all options.

Extrusion mounts require 2x M5 T-Nuts and 2x M5x10mm BHCS per rail. Since this is self explanatory we won’t show images of these options.

15

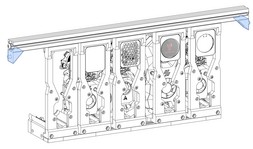
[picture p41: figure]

## M3x8mm BHCS

## M5x10mm BHCS

## M5 T-Nut

CORNER BRACKETS

These are a good idea either way, but specifically if top mounting it is highly recommended to add corner brackets on the top rail. The leverage of the docks will allow the rail to spin on the blind join, this will counter it.

## MOUNTING

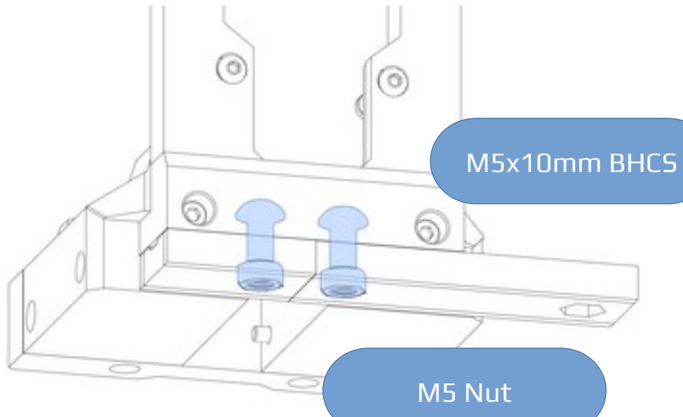
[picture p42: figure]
M5x10mm BHCS; M5 Nut

LINKS

Each dock will require 2 links. There are lots of combinations, the end piece has a single hole in it and is meant to start or end a chain of docks. Between docks there are different lengths, this is do to the size of and proper spacing between the tools/docks. The links are names to match the toolhead combinations to maintain the proper gap.

NOTE: Blackbird (BB) is the same length as SB.

NOTE: Links are strongly recommended as they add lots of stiffness across docks when no crossbar is available.

16

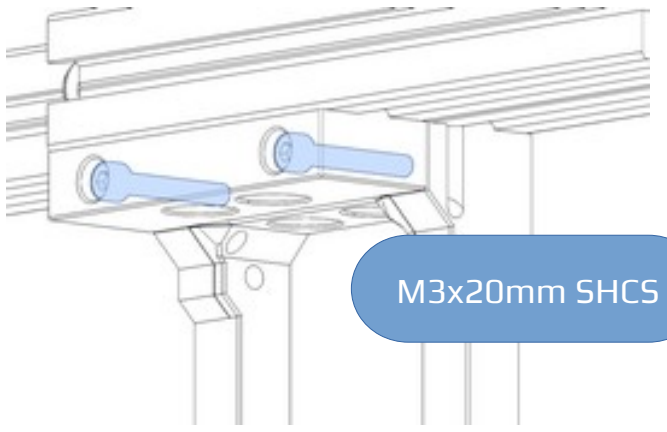
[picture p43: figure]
M3x20mm SHCS

BUFFER BRACKET

This is a special bracket to help secure the top part of the dock when used with the door buffer. It uses the L Bracket heat sets and screws into the printer top rail.

## CONTAINERS

OPTIONAL CONTAINER

Each dock can hold one optional container. There are several types and each type simply clips in. The container have the male side and the dock frame has the dimples at the top where they click into.

The blank version is provided for you to build off of it or if you want to add a tool ID to it. The grill version adds nice Voron style hexes to the top. The fancier version allow for electronics, there is a 3mm diameter wire path near the top of the frames to be able to safely run power to the top rail and across the docks.

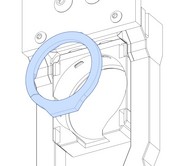
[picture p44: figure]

17

BLANK

GRILL

KNOMI

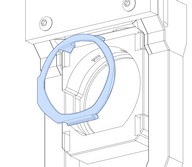
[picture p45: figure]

KNOMI V2

## SETUP TOOL

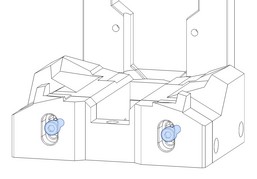
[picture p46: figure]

SETTING UP THE TOOL

There are 2 steps to this.

1. This step we want to make sure the tool sits at a perfect 90 degrees. Sit the tool into the dock and adjust the back plate (slotted bolts) until the dock can hold the tool at a perfect 90 degrees on it’s own. Make sure the tool is just inside the lip on the very back of the tool.
2. Once step 1 is fully done, we need to add M3 BHCS via the front to the front and screw them in. Optionally add 5x2 magnets to the head of the bolts on the front of the cowl (Steel bolts are required for this option). Tighten the bolts until it touches the bolts/magnets on the front cowl of the tool.

NOTE: Stealthburner shown, other tool heads user different screw sizes and placement.

18

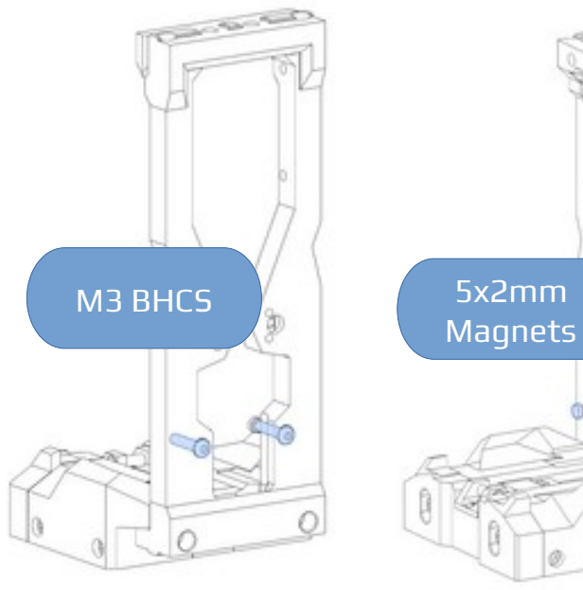
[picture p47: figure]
M3 BHCS; Magnets
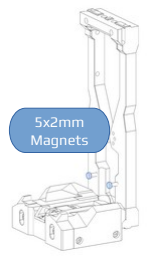
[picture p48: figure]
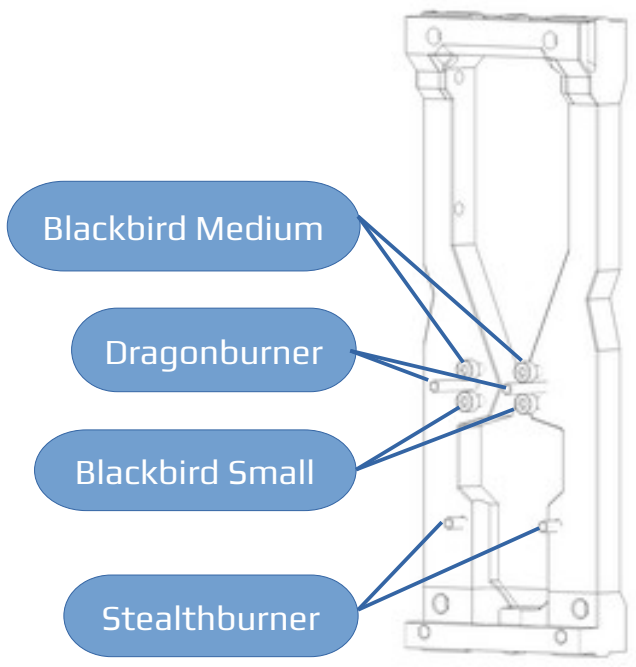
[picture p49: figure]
Blackbird Medium; Dragonburner; Blackbird Small; Stealthburner

## NEXT STEPS

ASSEMBLY COMPLETED!

Congratulations, now restart at Step 1 for as many tools as you are installing on your toolchanger.

### https://github.com/DraftShift/ModularDock/tree/main/config

NEXT STEP: CONFIGURATION

This manual is designed to be a reference manual for the build process of the Modular Dock.

The configuration you’ll require for the docking sequence can be found on our github page. We recommend starting there.

19

# DRAFTSHIFT DESIGN

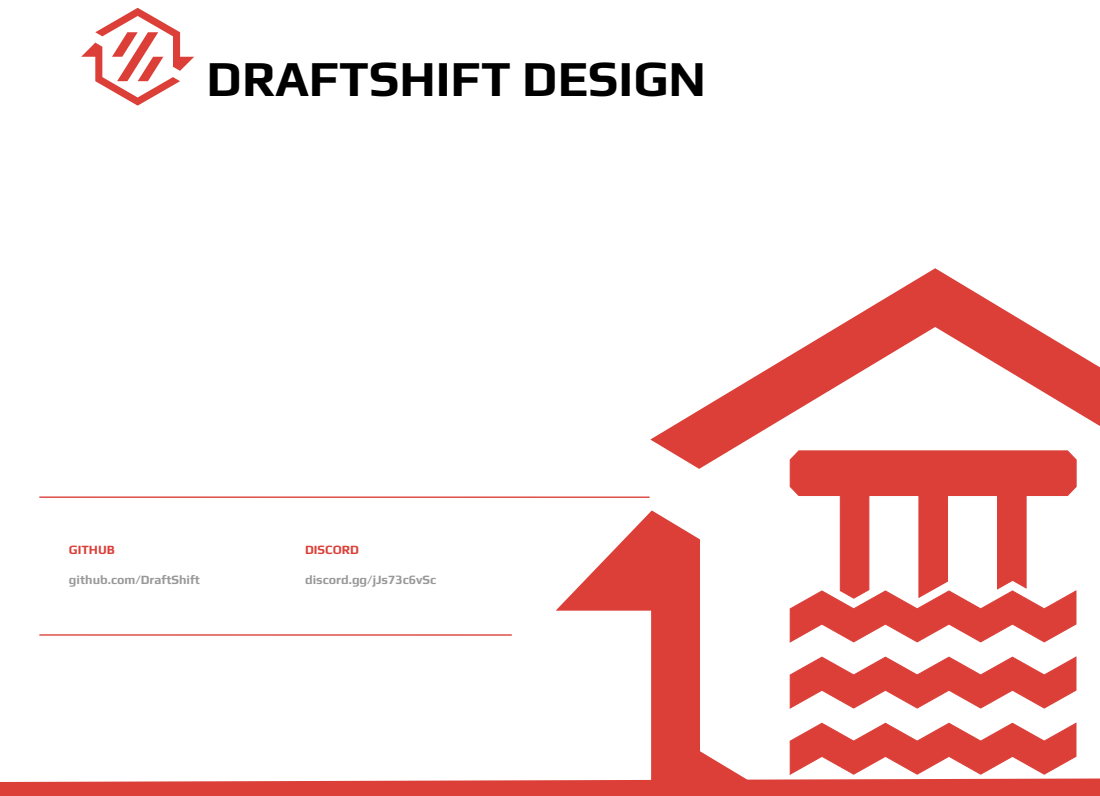
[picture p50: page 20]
DISCORD; discord.gg/jJs73c6vSc

GITHUB
github.com/DraftShift

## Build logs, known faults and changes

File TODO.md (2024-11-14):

# TODO

- [ ] Add a Halo Container
- [ ] Optional Brass Brush holder behind Wiper to brush as you pickup
- [ ] Optional Tray to catch what the brush drops (held by magnets for easy cleaning)
- [ ] Update Documentation

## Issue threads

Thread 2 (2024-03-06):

ptfe wiper doesn't have enough clearance to tighten the button head m3

GMBridge, 2024-03-06:
the ptfe wiper doesn't have enough clearance when the ptfe is installed to fit a 2mm ball end key into to tighten the m3 button head. can't tighten the m3 button head first, because then you can't install the ptfe segment.

TheSin-, 2024-04-28:
This was long fixed just forgot to close the issue

Closed 2024-04-28.

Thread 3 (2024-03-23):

Frame Left is missing a Hole in the STL

24Tigger24, 2024-03-23:

TheSin-, 2024-04-28:
Actually the Right one had an extra, this is fixed

Closed 2024-04-28.

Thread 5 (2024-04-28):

Will there also be a RapidBurner Dock version?

orotecluc, 2024-04-28:
Hi,
Congratz on your project, looks really great.
Only thing : I am not into 3D drawing, and am using RapidBurner toolheads (with G2SA extruders) and woul love to use your DoorSHift / Modular Dock to be able to have a toolchanging mechanism...
I currently have my toolheads printed with the Rapid Cowl as provided by Viesturz  [https://github.com/viesturz/tapchanger/tree/main/Tapchanger/STL/Toolheads/RapidBurner](https://github.com/viesturz/tapchanger/tree/main/Tapchanger/STL/Toolheads/RapidBurner)

TheSin-, 2024-05-01:
I'm hoping to add one, the issue with the taller tools is mixing, I'm working on that though.

TheSin-, 2024-09-22:
Added with https://github.com/DraftShift/ModularDock/commit/2ed60977f21839fce415b70efb9c046ddea14223

Closed 2024-09-22.

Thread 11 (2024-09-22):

Buffer bracket, where to find ?

bronsn, 2024-09-22:
Hello,
i try to build the Modular Dock with the Door Buffer mod.
In your manual under Mounting, you wrote:

_This is a special bracket to help secure the top part of the dock when used
with the door buffer. It uses the L Bracket heat sets and screws into the
printer top rail._

So, the Problem is, there is no Buffer Bracket at the stl files ?
Only a stl File named "top_crossbar", but this stl file doesnt have the holes to use with the L_bracket.

TheSin-, 2024-09-22:
That is old it’s replaced with the crossbar top and bottoms now it used to be 2 pieces

bronsn, 2024-09-22:
ty for the fast response, so with the new design i dont have to use , or cant use the L_bracket anymore ?

TheSin-, 2024-09-22:
No need for it with the crossbar top and bottom, it mostly just needed for top mounting

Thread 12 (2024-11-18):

Knomi 2 container issues

lindnjoe, 2024-11-18:
When you slice the knomi 2 container, it looses some of the outer walls.

TheSin-, 2024-11-18:
that seems to be more of a slicer issue, enable thin walls?

lindnjoe, 2024-11-24:
I got it to work, had to switch to a .2 nozzle and then it would slice without the missing walls. .4 nozzle and it would leave out the side walls.

TheSin-, 2024-11-24:
odd I run .4 and have no issues, still feel it's a slicer issue.

Glad you go it.

testack18, 2025-08-14:
For others who are running into the same issue. I had this as well. My slicer base profile is from Ellis's profile where the thin wall min with is 33%: thin_walls_min_width = 33% (SS profile setting)
I had to decrease this to 15% - 16% then the side thin walls were sliced correctly.
As this is a % value, the minimum may varies depends on your perimeter width settings. Check your G-Code preview before hit print.
I hope this helps other.

Closed 2024-11-24.

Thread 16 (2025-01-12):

Manual M5x8 screws should e M5x10

nic335, 2025-01-12:
As describe in title

Manual explain to use M5X8 for mounting the dock onto top and bottom extrusion.
In reality screws are too short, or not engaging enough thread for it being proper.

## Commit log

2024-03-03 Initial Commit of Pre Release Files
    [Back.stl, Base.stl, Base_Stubby.stl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]
2024-03-03 Fix the base mounting holes to match with the new frame location
    [Base.stl, Base_Stubby.stl]
2024-03-03 Adjust frame dimensions to reduce Z space usage. New README added
    [ShortFrame Left.stl, ShortFrame Right.stl]
2024-03-04 Add the Assembly manual
2024-03-04 Add BOM link
2024-03-04 Always get the brackets backwards
2024-03-04 Update the link bolt length to 16s and add a todo to make the links thicker
2024-03-04 Add note about Stubby dock 40mm screws. Thanks GMBridge.
2024-03-05 Add notes about corner brackets for top mounted docks
2024-03-05 Update Rail mounting bolts to use M5x10s instead for the less common M5x12s
    [Bottom.stl, Links.step, Top.stl]
2024-03-05 Update to make the links symetrical front and rear so the end links are the same
    [DB_to_DB.stl, DB_to_SB.stl, End.stl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]
2024-03-05 2 end links are require so follow proper naming, Thanks GMBridge
    [End_x2.stl]
2024-03-05 Link bolt is 10mm not 16mm, Thanks Marc
2024-03-06 add a note that the stubby DB base is not compatible with an extended front frame
2024-03-07 Update PTFE Wiper
    [PTFE_Option.stl]
2024-03-08 Update bolt size for the cup wiper
2024-03-08 New PTFE wiper and better magnet holes on the back pieces
    [Back.stl, PTFE_Option.stl]
2024-03-09 Add the mold for the String Steel Wiper
    [Nozzle Pad Mold A.stl, Nozzle Pad Mold B.stl]
2024-03-09 Add a bracket to attach the frame to a 2020 that is behind the top piece
    [Buffer_Bracket.stl]
2024-03-09 Rename to fix typo
    [L_Bracket.stl]
2024-03-10 New SB Base/Back, Update Frame for new BB adjusters, Remove top SB adjusters, resave all stls to proper print orientation
    [Back.stl, Base.stl, Base_Stubby.stl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]
2024-04-23 Update CAD and STLs to the latest, documentation still need to be redone
    [Back.stl, Base.stl, Base_Stubby.stl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]
2024-04-28 Knomi2 Mod
    [Knomi2.step, frame.stl, ring.stl]
2024-05-01 Updated to new frame
    [Knomi2.step, frame.stl, ring.stl]
2024-05-02 Update Blackbird to new upstream ducts, move Knomi2 out of WIP since it's been tested
    [Base.stl, [a]_Knomi2.stl, [a]_Knomi2_Ring.stl]
2024-05-03 Add XOL
    [Back.stl, Base.stl, Left.stl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]
2024-05-03 Add missing Chamfers
    [Left.stl, Right.stl]
2024-05-03 Deal with space issue on some shuttles
    [Back.stl, PTFE_Option.stl]
2024-05-14 Rework BB, SB, XOL docks to be 76mm instead of 80mm
    [Back.stl, Base.stl]
2024-05-19 Updated ShortFrame To current design
    [ShortFrame Left.stl, ShortFrame Right.stl]
2024-05-29 Fix the L Bracket hole size, thanks Arthur le Daron
    [L_Bracket.stl]
2024-05-29 Door not Frame
2024-06-28 Improve BOM readability
2024-07-06 Update BOM
2024-07-06 Add Short Frame and MiniSB docks
    [Back.stl, Base.stl, Base_Stubby.stl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]
2024-07-21 Fix order for magnets
2024-07-30 Fix a mistake in the stubby cup main body that limited movement of the cup
    [Cup_Stubby_Body.stl]
2024-08-19 Add Monolith Crossbar
    Add Monolith Crossbar
    [DockBar_MonolithAWD_bracket_V2.1_A.step, DockBar_MonolithAWD_bracket_V2.1_A.stl, DockBar_MonolithAWD_bracket_V2.1_B.step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]
2024-08-20 Update DB Design for new backplate for better docking, add Yavoth and it's stubby
    [Back.stl, Back_Legacy.stl, Base.stl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]
2024-08-20 Add Yavoth to BOM
2024-08-20 Add extra magnets for Yavoth
2024-08-22 Correct the magnet holes in the Yavoth
    [Base.stl, Base_Stubby.stl]
2024-09-04 Update to 8s incase, some extrusions aren't as deep it seems
2024-09-04 notes about frame size and crossbar versions
2024-09-22 Add support for RapidBurner
    [Left.stl, Right.stl]
2024-10-06 Move Blockers to there own directory
    [Cup.stl, Cup_Body.stl, Cup_Stubby_Body.stl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]
2024-10-14 Fix minor issue
    [Base.stl]
2024-10-15 New cup with more travel, new PTFE wiper and backplates for the new wiper
    [Back.stl, Back_Legacy.stl, BambuNozzleWiper.step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]
2024-10-15 Rename to size since we have so many tools now
    [60_to_60.stl, 80_to_60.stl, 80_to_80.stl]
2024-11-14 Add Rear Link system, new mount points for a future addon, A4T and Anthead docks
    [Back.stl, Base.stl, Base_Stubby.stl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]
2024-12-02 A4T magnet dock initial commit
    [A4T_Upright_Short_Left.STL, A4T_Upright_Short_Right.stl]
2024-12-02 Added A4T CAD
    [A4T_Magnet_Dock_Upright_Left.STEP, A4T_Magnet_Dock_Upright_Right.STEP]
2024-12-30 add usermod xol-toolhead magnet dock adapter
    add usermod xol-toolhead magnet dock adapter
    [Xol_SC_Magdock_Faceplate_SC_Logo_Diffusor.step, Xol_SC_Magdock_Faceplate_SC_Logo_Diffusor.stl, Xol_SC_Magdock_Faceplate_SC_Logo_with_cutouts.step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]
2025-02-16 Update anthead docks to allow for led ducts
    [Base.stl, Base_Stubby.stl]
2025-03-14 Adding spring steel pad mold (#18)
    Creating Spring Steel Pad molds CAD from STLs.
    [Spring Steel Pad Mold.step]
2025-04-20 add xol magdock feetmags usermod (#20)
    add xol magdock feetmags usermod
    [DSD_Modular_Dock_Back_XOL_Feetmags.stl, DSD_Modular_Dock_Back_XOL_nf_Feetmags.step, SC_XOL_Feetmags_UHF.step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]
2025-06-14 M5x10 instead of M5x8, (#17)
    Fix Bom error, M5x10 instead of M5x8 for 2020 extrusions is required.
    1515 remain the same M3x8
2025-06-14 Adding Spring Cub Blocker user mod (#19)
    [Spring Cup Blocker.stl]
